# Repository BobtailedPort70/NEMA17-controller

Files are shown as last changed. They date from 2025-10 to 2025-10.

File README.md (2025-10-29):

# NEMA17 Controller
A compact controller for NEMA17 stepper motors, with CAN and I2C communication protocols.

## Pictures
### PCB


### Enclosure


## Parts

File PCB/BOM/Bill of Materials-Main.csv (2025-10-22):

Comment | Description | Designator | Footprint | LibRef | Quantity
15 pF | CAP CER 15PF 50V C0G/NP0 0402 | C1, C2 | CAP 0402_1005 | CBR04C150J5GAC | 2
100 pF | CAP CER 100PF 50V C0G/NP0 0402 | C3, C4 | CAP 0402_1005 | 500X07N101MV4T | 2
0.1 µF | CAP CER 0.1UF 16V X7R 0402 | C5, C7, C8, C9, C11, C12, C13, C14, C15, C17, C26, C27, C30, C31, C32 | CAP 0402_1005 | CL05B104KO5NFNC | 15
10 µF | CAP CER 10UF 10V X5R 0402 | C6 | CAP 0402_1005 | CL05A106MP8NUB8 | 1
1 µF | CAP CER 1UF 16V X7R 0603 | C10 | CAP 0603_1608 | C0603C105K4RACAUTO | 1
100µF | CAP ALUM 100UF 20% 6.3V SMD | C16 | CAP ALSMD 6.6MM H5.4MM | EEE-FC0J101P | 1
0.022µF | CAP CER 0.022UF 50V X7R 0402 | C18 | CAP 0402_1005 | 0402YC223KAT2A | 1
10000 pF | CAP CER 0402 10NF 50V X7R 20% | C19 | CAP 0402_1005 | C0402C103M5RECAUTO | 1
1 µF | CAP CER 1UF 10V X7S 0402 | C20, C23 | MURATA GRM155 0402_1005 | GRM155C71A105KE11D | 2
22 µF | CAP CER 22UF 10V X5R 0603 | C21 | CAP 0603_1608 | C1608X5R1A226M080AC | 1
4.7 µF | CAP CER 4.7UF 16V X5R 0402 | C22 | CAP 0402_1005 | CL05A475MO5NUNC | 1
10 µF | CAP CER 10UF 6.3V X5R 0603, CAP CER 10UF 35V X5R 0603 | C24, C25, C28, C29 | MURATA GRM188 0603_1608 | GRM188R60J106ME47D, GRM188R6YA106MA73D | 4
Red | LED RED CLEAR CHIP SMD | D1 | LED 0603_1608 RED | LSM0603412V | 1
Yellow | LED YELLOW CLEAR CHIP SMD | D2 | LED 0603_1608 YELLOW | LSM0603472V | 1
B5819WS-TP | DIODE SCHOTTKY 40V 1A SOD323 | D3 | SOD323 | B5819WS-TP | 1
SMF30A | TVS SOD123FL 30V 200W UNIDIR | D4, D5 | SOD123F | SMF30A | 2
USBLC6-2P6 | TVS DIODE 5.25V 17V SOT666 | D6 | FP-SOT-666-MFG | CMP-12225-000058-1 | 1
120 Ohms @ 100 MHz | FERRITE BEAD 120 OHM 0402 1LN | FB1 | FER 0402_1005 | BLM15PX121SN1D | 1
RY8310 | Integrated Circuit | IC1 | SOT95P280X145-6N | RY8310 | 1
B6B-PH-K(LF)(SN) | CONN HEADER VERT 6POS 2MM | J1, J2 | JST B6B-PH-K | B6B-PH-K(LF)(SN) | 2
1054500101 | CONN RCP USB3.1 TYPEC 24P SMD RA | J3 | Molex 1054500101 | 1054500101 | 1
4.7 µH | FIXED IND 4.7UH 1.3A 260MOHM SMD | L1 | TAIYO YUDEN MAMK2520T1R0M | MAMK2520T4R7M | 1
61300411121 |  | P1, P2 | 61300411121 | CMP-1502-01064-3 | 2
XC6206P332MR-G | Power Supply | PS1 | SOT95P280X130-3N | XC6206P332MR-G | 1
120 Ohms | RES SMD 120 OHM 5% 0.4W 0805 | R1 | RES 0805_2012 | ESR10EZPJ121 | 1
20 kOhms | RES SMD 20K OHM 0.1% 1/16W 0402 | R2, R7, R8, R11, R13 | RES 0402_1005 | CPF0402B20KE | 5
10 kOhms | RES 10K OHM 0.1% 1/16W 0603 | R3, R4 | RES 0603_1608 | RNCS0603BKE10K0 | 2
1.5 kOhms | RES SMD 1.5K OHM 5% 1/16W 0402 | R5, R6, R19 | YAGEO RES 0402_1005 | AC0402JR-071K5L | 3
0 Ohms | RESA-AS 0603 0R JUMPER 100MW | R9 | RES 0603_1608 | CR0603AJ/-000EAS | 1
110 mOhms | RES 0.11 OHM 1% 1/3W 0805 | R10, R12 | RES 0805_2012 | RL1220S-R11-F | 2
3313J-1-203E | 3 mm Trimpot(R) Trimming Potentiometer, 20 KOhm, +/- 20%, 0.125 W, -55 to 125 degC, 3-Pin SMD, RoHS, Tape and Reel | R14 | BOUR-3313J-1_V | CMP-2000-05586-1 | 1
43 kOhms | RES 43K OHM 5% 1/16W 0402 | R15 | YAGEO RES 0402_1005 | RC0402JR-0743KL | 1
8.2 kOhms | RES SMD 8.2K OHM 1% 1/10W 0402 | R16 | RES 0402_1005 | ERJ-2RKF8201X | 1
5.1 kOhms | RES SMD 5.1K OHM 0.1% 1/16W 0402 | R17, R18 | YAGEO RES 0402_1005 | RT0402BRE075K1L | 2
KMR211GLFS | SWITCH TACTILE SPST-NO 0.05A 32V | SW1 | FP-KMR211GLFS-MFG | CMP-10040-000023-1 | 1
TJA1044GTK/3Z | No Description Available | U1 | SON8_TJA1044GTK3Z_NXP | TJA1044GTK3Z | 1
STM32F103C8T6 | ARM Cortex-M3 32-bit MCU, 64 KB Flash, 20 KB Internal RAM, 37 I/Os, 48-pin LQFP, -40 to 85 degC, Tray | U2 | STM-LQFP48_L | CMP-0237-00215-3 | 1
TMC2209-LA | Bipolar Motor Driver Power MOSFET Step/Direction, UART 28-QFN (5x5) | U3 | QFN50P500X500X90-29N | CMP-020-00024-1 | 1
X322516MLB4SI | External dimensions: 3.2 x 2.5 x 0.8 mm.Frequency range: 11.0592MHz ~54MHz | Y1 | OSC_X322516MLB4SI | CMP-003-00030-1 | 1

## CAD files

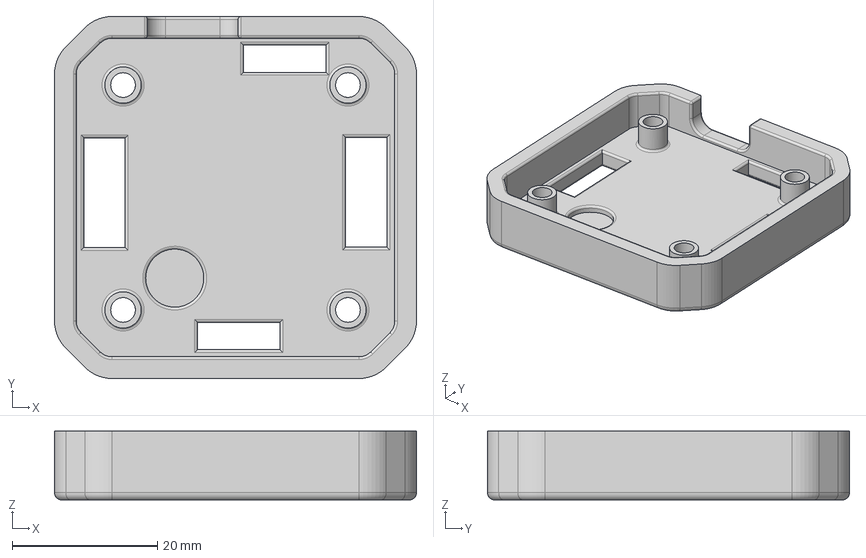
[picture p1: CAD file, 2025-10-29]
Enclosure/NEMA17-controller-enclosure-V2/NEMA17-controller-enclosure-bottom - Part 2.step
49.9 x 49.9 x 9.50 mm

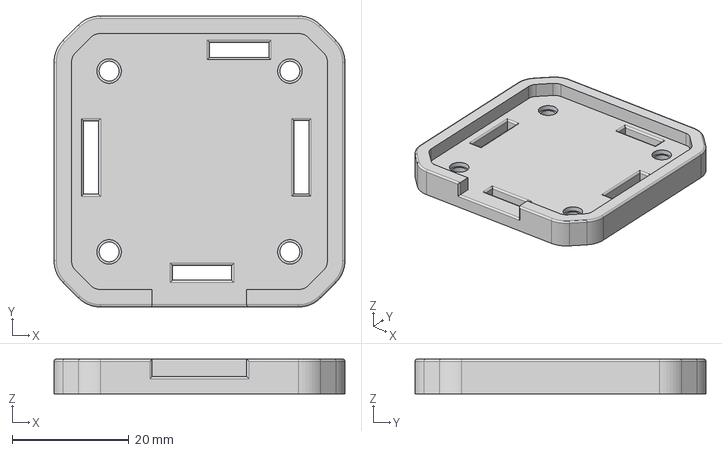
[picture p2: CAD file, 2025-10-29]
Enclosure/NEMA17-controller-enclosure-V2/NEMA17-controller-enclosure-top - Part 2.step
49.9 x 49.9 x 6.00 mm

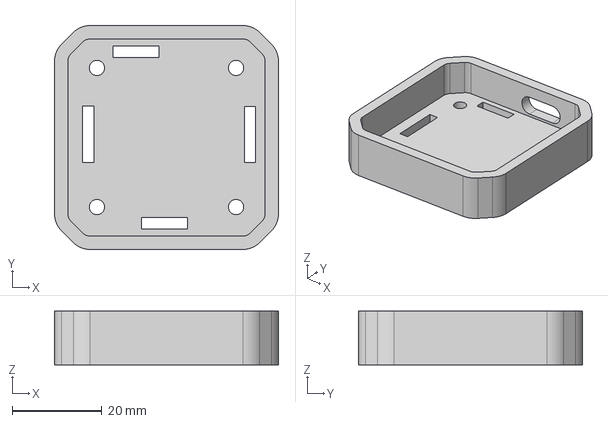
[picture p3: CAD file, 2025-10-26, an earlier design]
Enclosure/NEMA17-controller-enclosure-V1/NEMA17-controller-enclosure-bottom - Part 1.step
49.9 x 49.9 x 12.0 mm

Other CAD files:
Enclosure/NEMA17-controller-enclosure-V1/NEMA17-controller-enclosure-bottom - Part 1.stl
Enclosure/NEMA17-controller-enclosure-V2/NEMA17-controller-enclosure-bottom - Part 2.sldprt
Enclosure/NEMA17-controller-enclosure-V2/NEMA17-controller-enclosure-top - Part 2.sldprt
Enclosure/NEMA17-controller-enclosure-V2/NEMA17-controller-enclosure-top - Part 2.stl

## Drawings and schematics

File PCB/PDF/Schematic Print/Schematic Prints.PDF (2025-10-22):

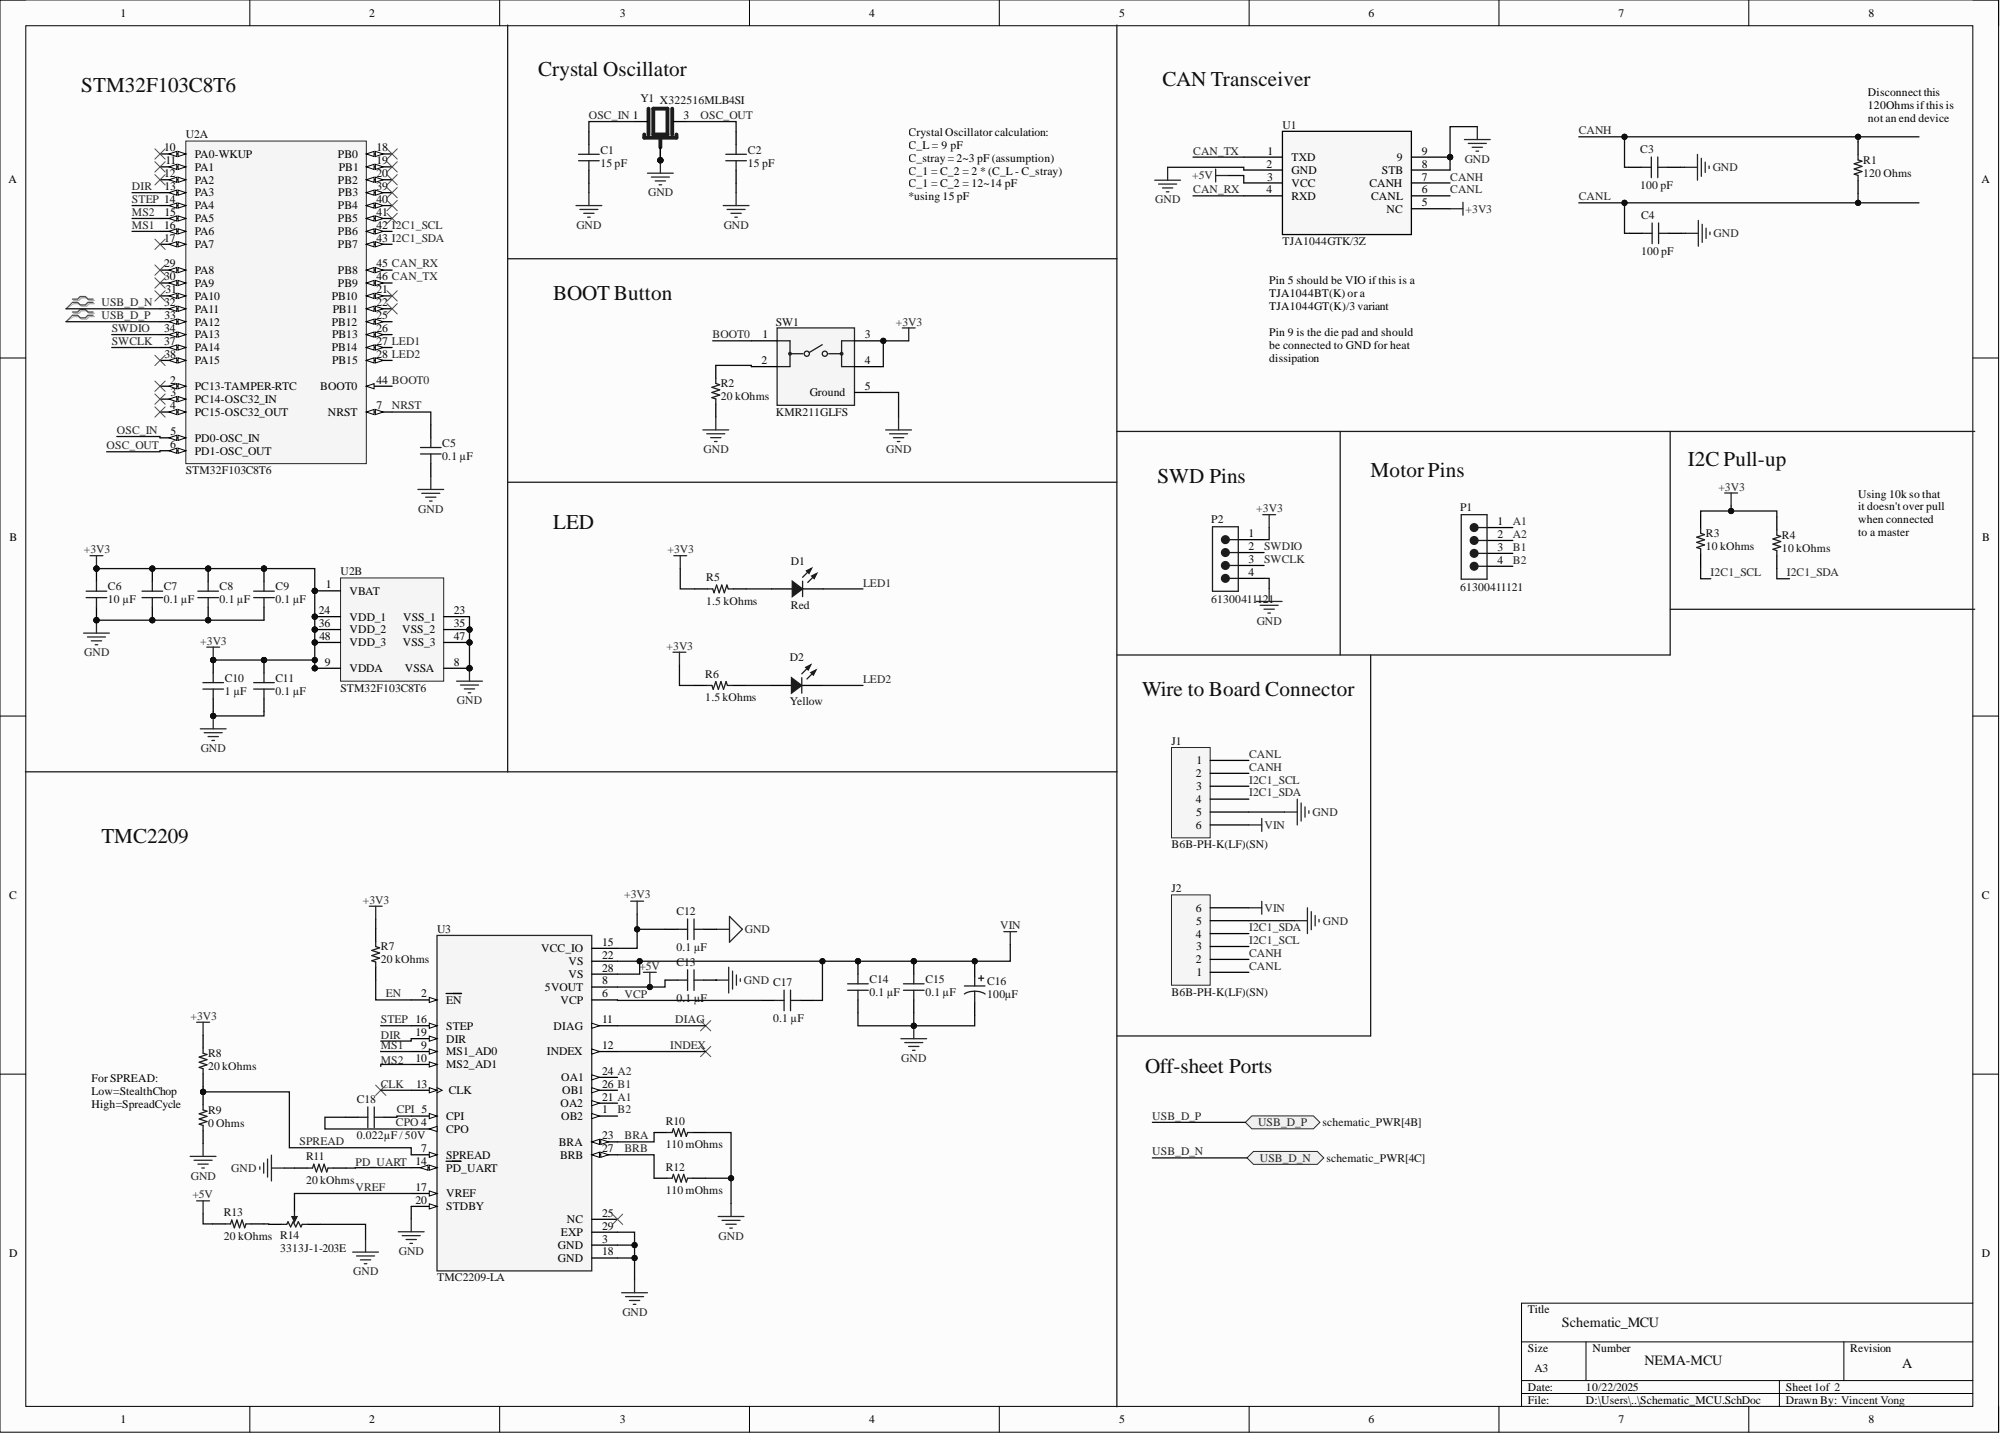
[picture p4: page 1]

3 6 | 3 5
4 8 | 4 7

Wire to Board Co

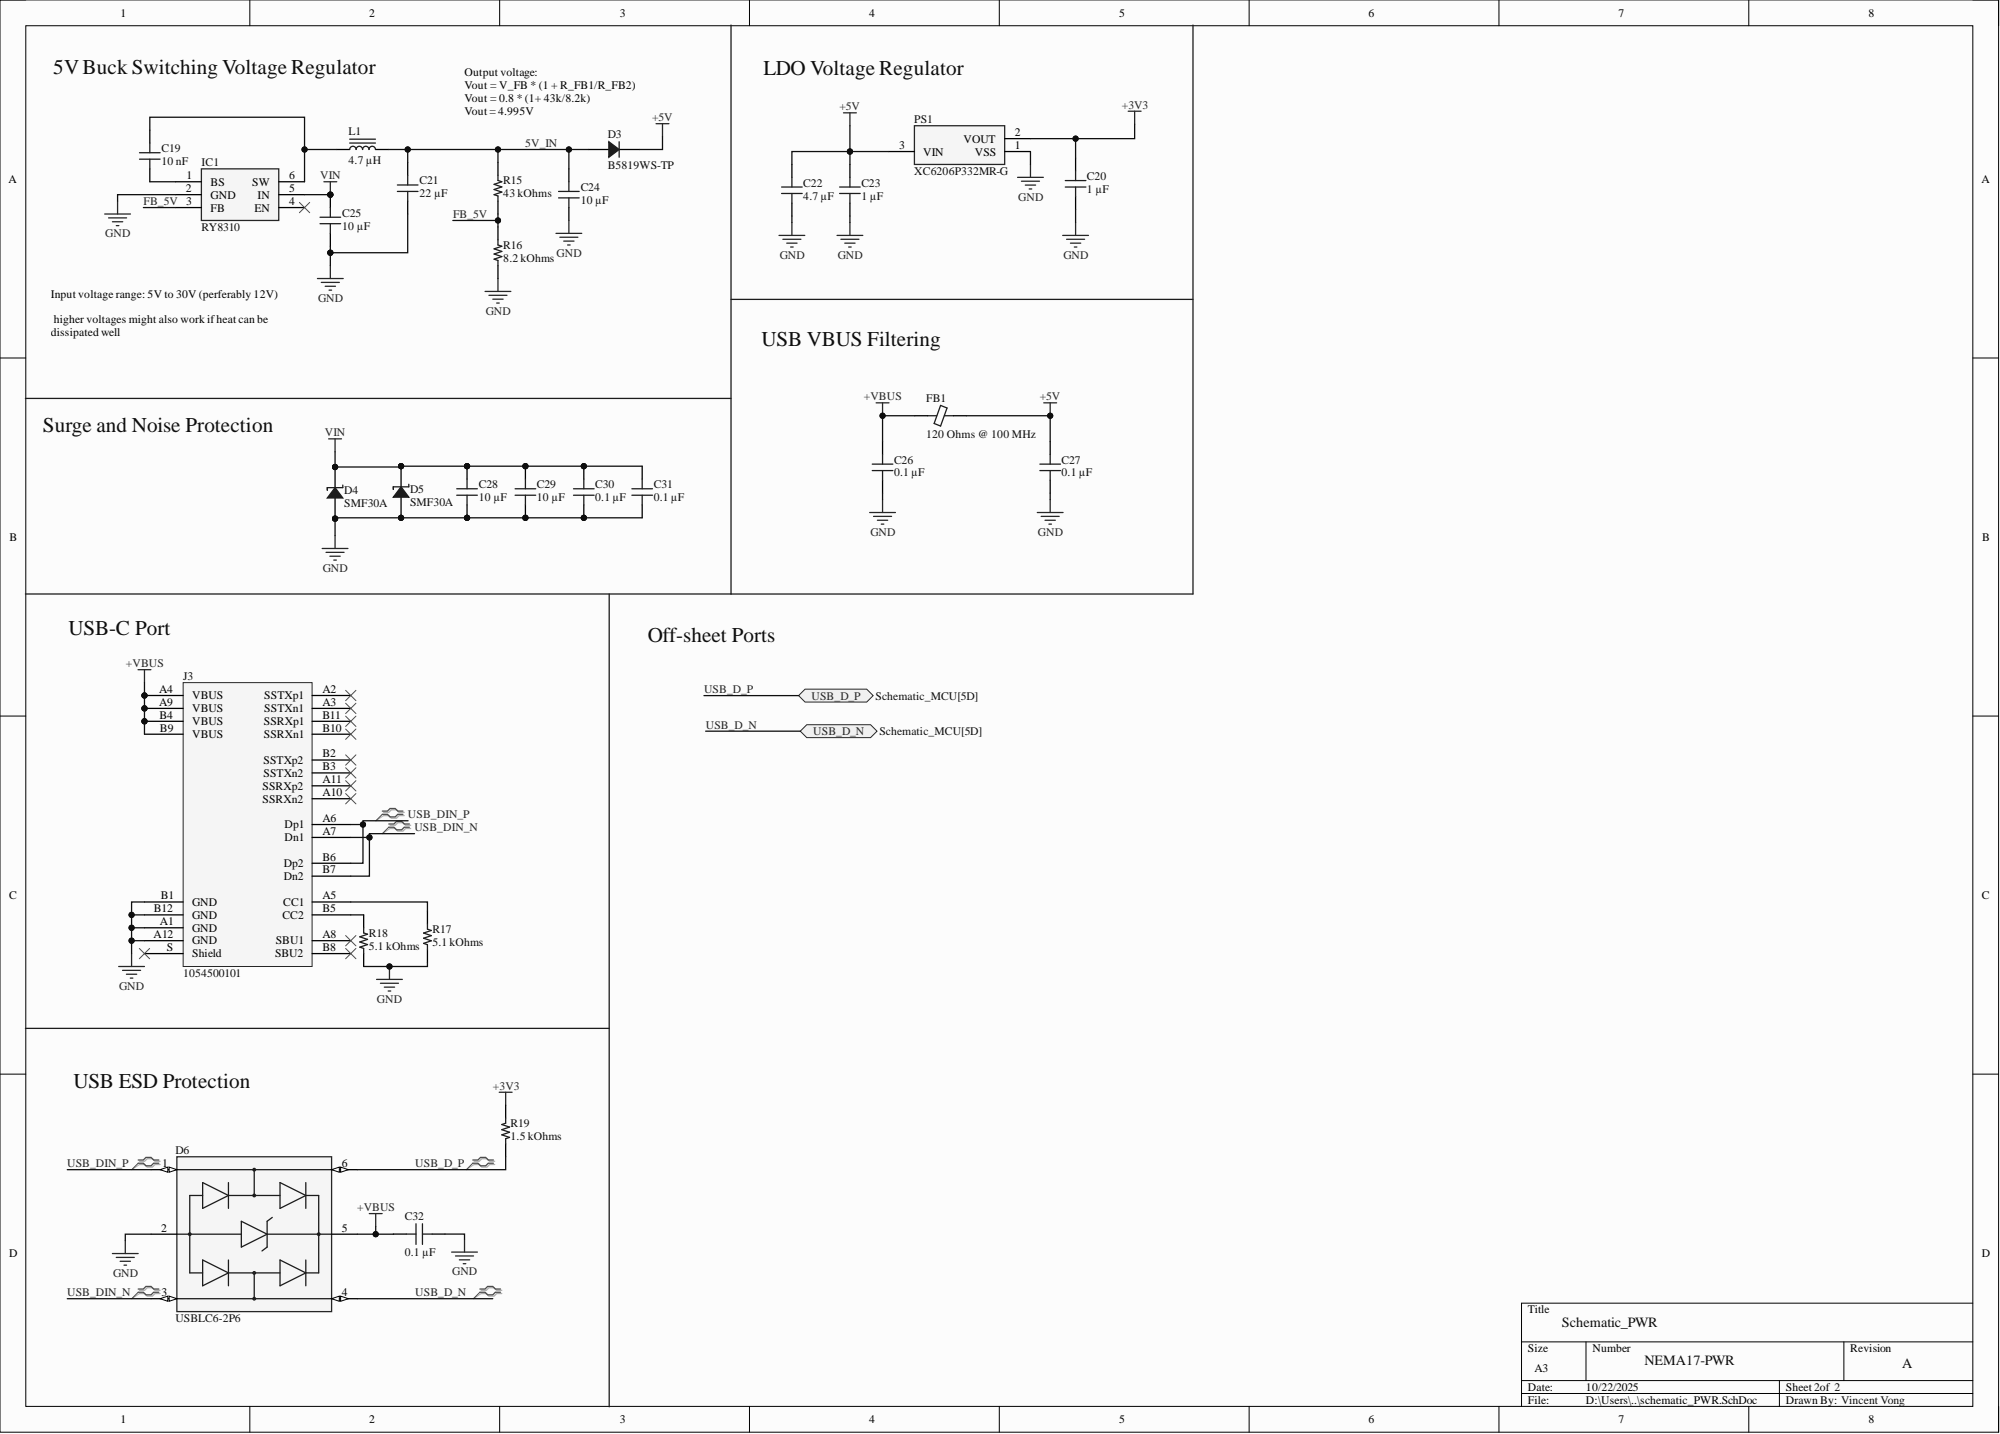
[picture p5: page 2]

5V Buck Switching Voltage Regulator

Input voltage range: 5V to 30V (perferably 12V)

higher voltages might also work if heat can be
dissipated well

Surge and Noise Protection

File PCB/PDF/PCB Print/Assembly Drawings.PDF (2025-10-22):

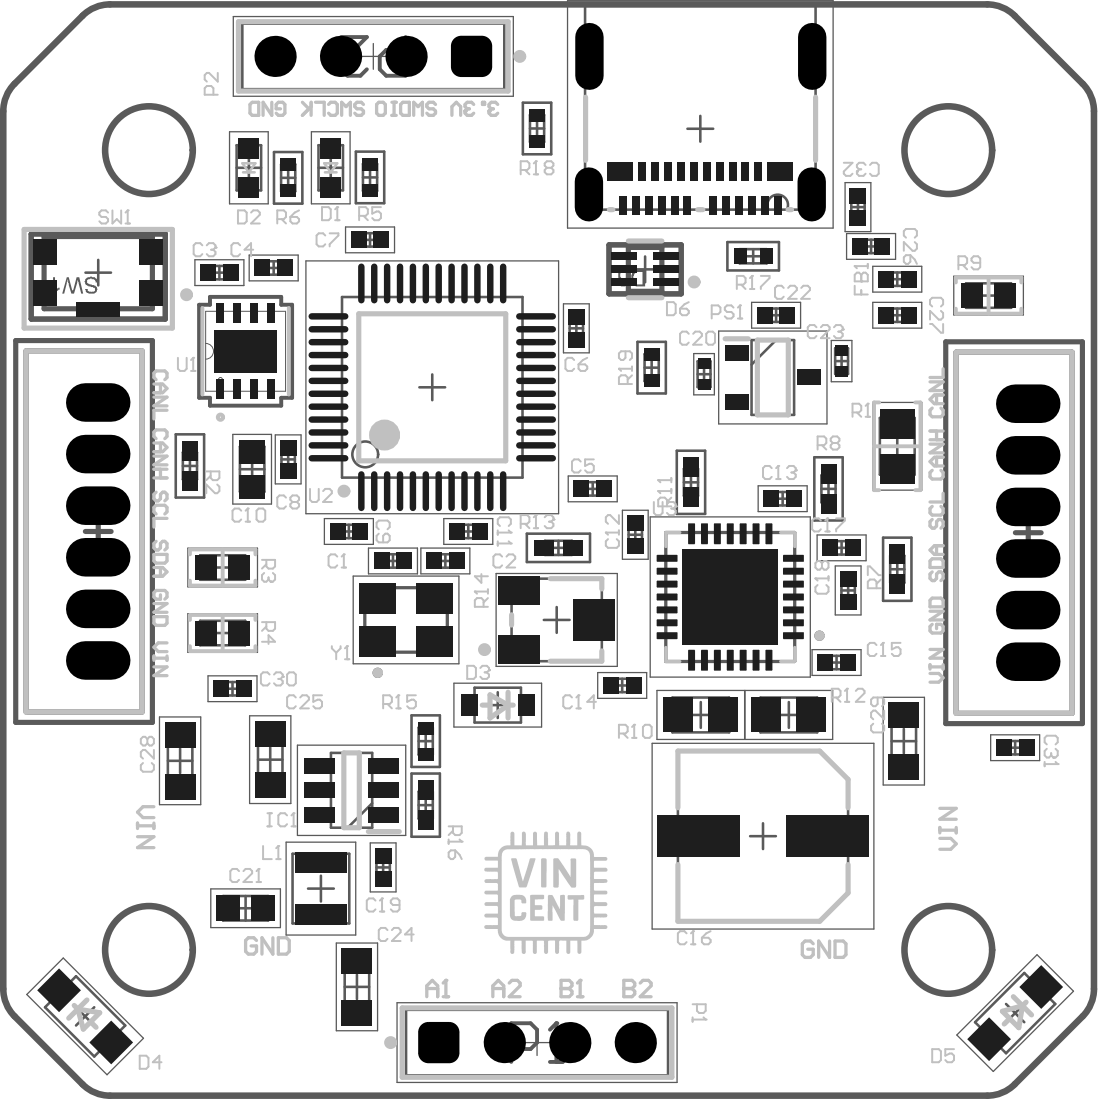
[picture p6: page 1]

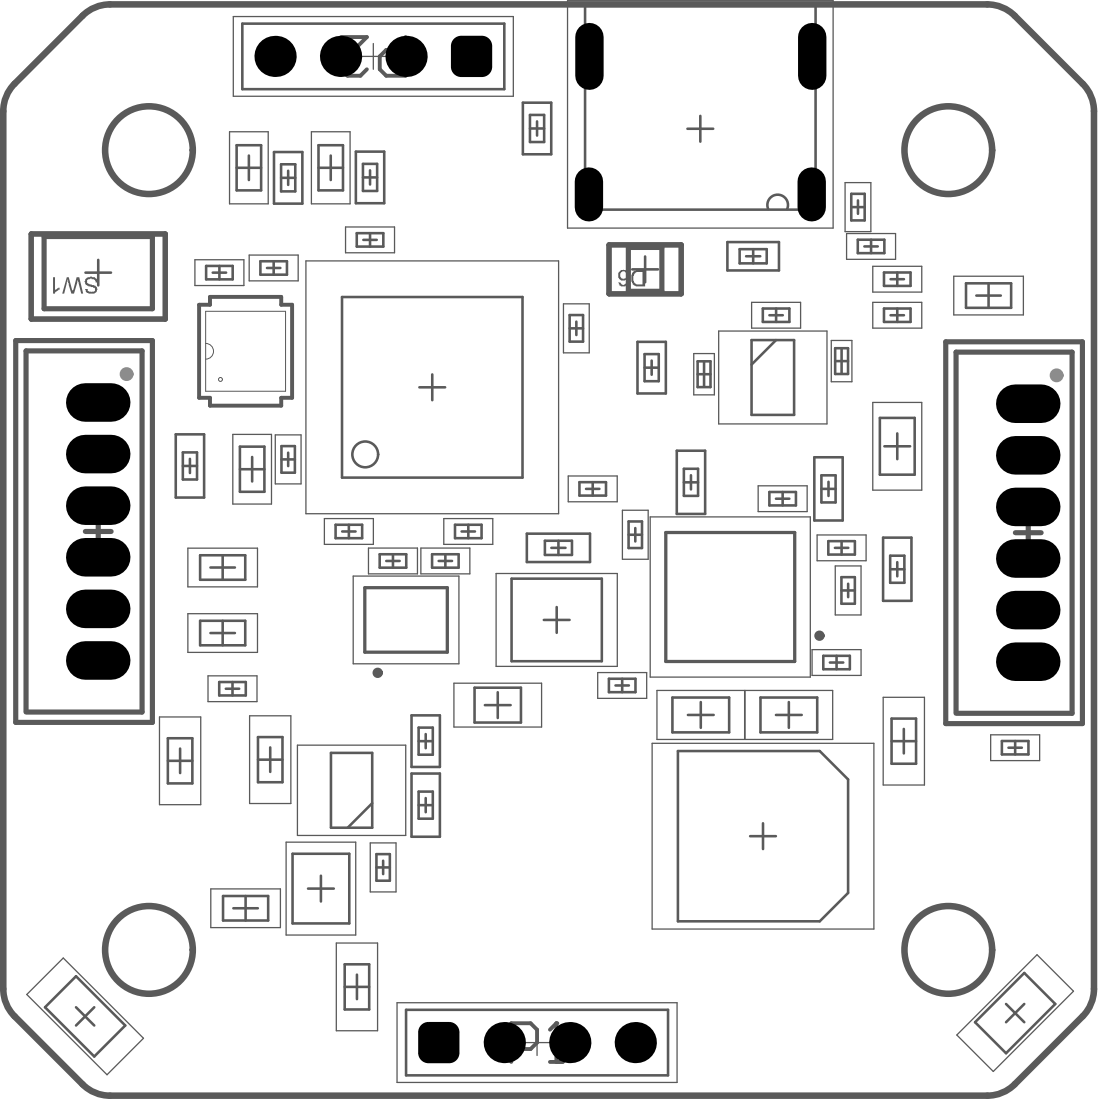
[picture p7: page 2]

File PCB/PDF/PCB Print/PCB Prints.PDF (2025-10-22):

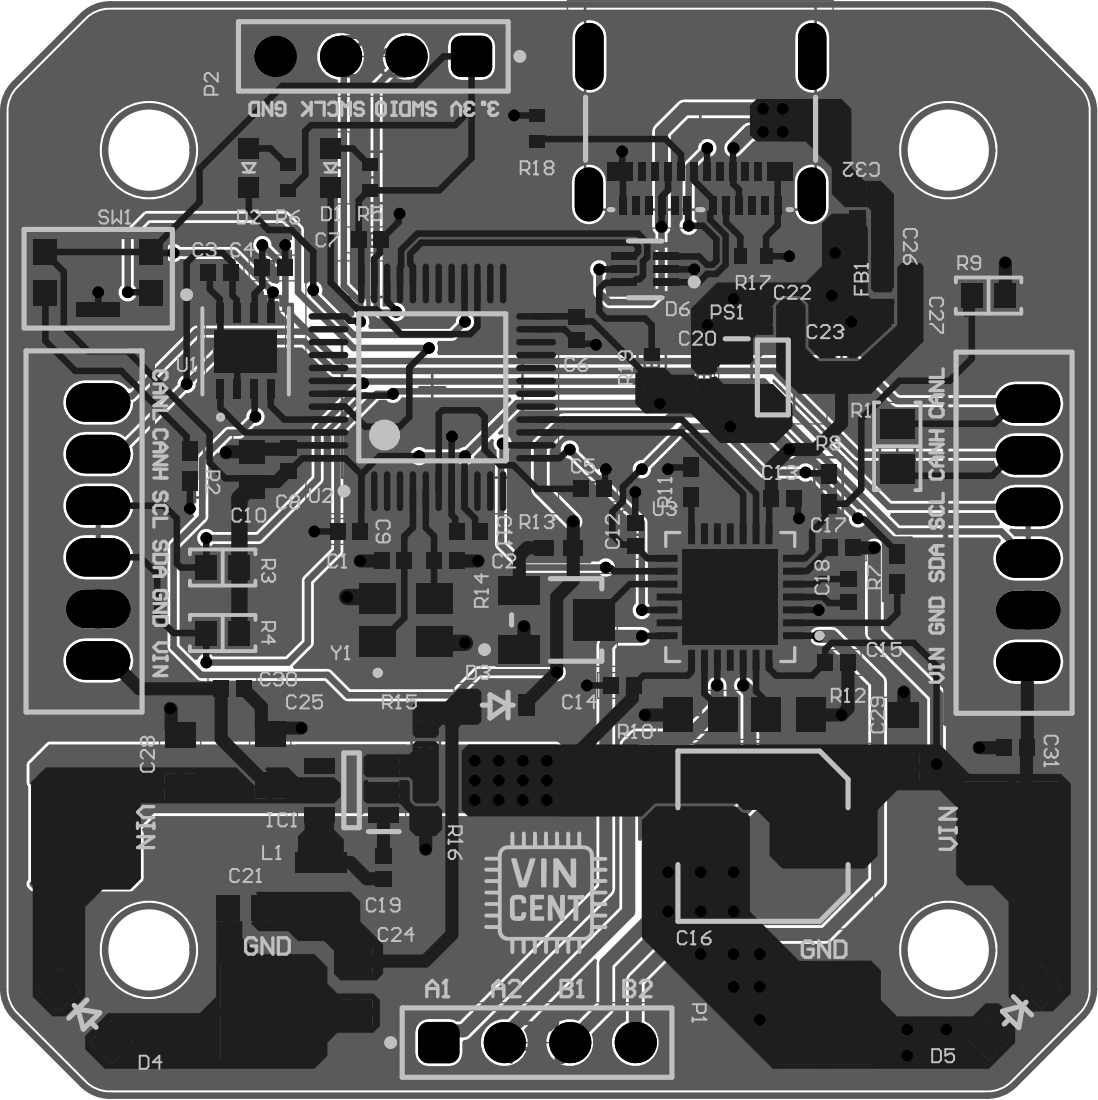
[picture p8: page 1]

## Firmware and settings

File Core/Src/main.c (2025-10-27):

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
/* Includes ------------------------------------------------------------------*/
#include "main.h"
#include "stm32f1xx_hal.h"
#include "usb_device.h"

/* USER CODE BEGIN PM */
#define STEP_WRITE(x) HAL_GPIO_WritePin(STEP_GPIO_Port, STEP_Pin, (x)?GPIO_PIN_SET:GPIO_PIN_RESET)
#define DIR_FWD()     HAL_GPIO_WritePin(DIR_GPIO_Port,  DIR_Pin,  GPIO_PIN_SET)
#define DIR_REV()     HAL_GPIO_WritePin(DIR_GPIO_Port,  DIR_Pin,  GPIO_PIN_RESET)
//#define EN_ON()       HAL_GPIO_WritePin(EN_GPIO_Port,   EN_Pin,   GPIO_PIN_RESET)
//#define EN_OFF()      HAL_GPIO_WritePin(EN_GPIO_Port,   EN_Pin,   GPIO_PIN_SET)

/* USER CODE END PM */

CAN_HandleTypeDef hcan;

I2C_HandleTypeDef hi2c1;

TIM_HandleTypeDef htim2;

/* USER CODE BEGIN PV */
uint8_t RX_Buffer [1] ; // DATA to receive

/* USER CODE END PV */

void SystemClock_Config(void);
static void MX_GPIO_Init(void);
static void MX_CAN_Init(void);
static void MX_I2C1_Init(void);
static void MX_TIM2_Init(void);
/* USER CODE BEGIN 0 */
static inline void delay_us(uint32_t us)
{
    uint16_t start = __HAL_TIM_GET_COUNTER(&htim2);
    while ((uint16_t)(__HAL_TIM_GET_COUNTER(&htim2) - start) < us) {
        //__NOP();
    }
}

static inline void STEP_PULSE_US(uint16_t high_us, uint16_t low_us)
{
    STEP_WRITE(1);
    delay_us(high_us);
    STEP_WRITE(0);
    delay_us(low_us);
}

void Stepper_MoveSteps(uint32_t steps, int dir, uint16_t step_high_us, uint16_t step_low_us)
{
    if (dir >= 0) { DIR_FWD(); } else { DIR_REV(); }

    //EN_ON();                 // TMC2209 enable is active-low
    delay_us(10);            // tiny settle

    for (uint32_t i = 0; i < steps; i++) {
        STEP_PULSE_US(step_high_us, step_low_us);
    }

    //EN_OFF();                // optional: disable when done
}

/* USER CODE END 0 */

/**
  * @brief  The application entry point.
  * @retval int
  */
int main(void)
{

  /* MCU Configuration--------------------------------------------------------*/

  /* Reset of all peripherals, Initializes the Flash interface and the Systick. */
  HAL_Init();

  /* Configure the system clock */
  SystemClock_Config();

  /* Initialize all configured peripherals */
  MX_GPIO_Init();
  MX_CAN_Init();
  MX_I2C1_Init();
  MX_USB_DEVICE_Init();
  MX_TIM2_Init();
  /* USER CODE BEGIN 2 */
  HAL_TIM_Base_Start(&htim2);  // start 1 MHz timer
  HAL_I2C_Slave_Receive_IT(&hi2c1 ,(uint8_t *)RX_Buffer, 1); //Receiving in Interrupt mode
  HAL_Delay(100);

  // One-time initial states (run once after init)
  DIR_FWD();         // set default direction
  STEP_WRITE(0);     // make sure STEP starts low
  HAL_GPIO_WritePin(LED2_GPIO_Port, LED2_Pin, GPIO_PIN_SET); // Turn on LED2 to indicate ready

  /* USER CODE END 2 */

  /* Infinite loop */
  /* USER CODE BEGIN WHILE */
  while (1)
  {
    HAL_GPIO_TogglePin(LED1_GPIO_Port, LED1_Pin); // Toggle LED1
    HAL_Delay(100);
    HAL_GPIO_TogglePin(LED2_GPIO_Port, LED2_Pin); // Toggle LED2
    HAL_Delay(100);

    

    /* USER CODE END WHILE */

    /* USER CODE BEGIN 3 */
    Stepper_MoveSteps(1600, +1, 3, 997);  // ~1 kHz steps, 3 µs high
    HAL_Delay(500);
    Stepper_MoveSteps(1600, -1, 3, 997);
    HAL_Delay(500);
  }
  /* USER CODE END 3 */
}

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


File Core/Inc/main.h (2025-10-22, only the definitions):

#define DIR_Pin GPIO_PIN_3
#define DIR_GPIO_Port GPIOA
#define STEP_Pin GPIO_PIN_4
#define STEP_GPIO_Port GPIOA
#define MS2_Pin GPIO_PIN_5
#define MS2_GPIO_Port GPIOA
#define MS1_Pin GPIO_PIN_6
#define MS1_GPIO_Port GPIOA
#define LED1_Pin GPIO_PIN_14
#define LED1_GPIO_Port GPIOB
#define LED2_Pin GPIO_PIN_15
#define LED2_GPIO_Port GPIOB

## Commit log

2025-10-22 Add project description to README
    Add project description for NEMA17 stepper motor controller
2025-10-22 Add PCB manufacturing files and documentation.
    [Bill of Materials-Main.csv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]
2025-10-26 added step and STL files for enclosure bottom V1
    [NEMA17-controller-enclosure-bottom - Part 1.step, NEMA17-controller-enclosure-bottom - Part 1.stl]
2025-10-26 Enhance README with pictures of PCB and enclosure
    Added images of the PCB and enclosure to the README.
2025-10-26 chore: Update main.c and add enclosure files added step and STL files for enclosure bottom V1
    [NEMA17-controller-enclosure-bottom - Part 1.step, NEMA17-controller-enclosure-bottom - Part 1.stl]
2025-10-27 Added stepper motor movement
2025-10-29 Add new enclosure image to README
2025-10-29 Added NEMA17 controller enclosure V2 files
    [NEMA17-controller-enclosure-bottom - Part 2.sldprt, NEMA17-controller-enclosure-bottom - Part 2.step, NEMA17-controller-enclosure-top - Part 2.sldprt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]
2025-10-29 modified top enclosure part file
    [NEMA17-controller-enclosure-top - Part 2.sldprt, NEMA17-controller-enclosure-top - Part 2.step, NEMA17-controller-enclosure-top - Part 2.stl]
2025-10-29 Corrected hole alignment for capacitor
    [NEMA17-controller-enclosure-bottom - Part 2.sldprt, NEMA17-controller-enclosure-bottom - Part 2.step]
2025-10-29 modified face plate dimensions
    [NEMA17-controller-enclosure-bottom - Part 2.sldprt, NEMA17-controller-enclosure-bottom - Part 2.step, NEMA17-controller-enclosure-top - Part 2.sldprt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]

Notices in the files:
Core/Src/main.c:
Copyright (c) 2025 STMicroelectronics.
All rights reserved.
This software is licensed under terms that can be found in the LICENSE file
